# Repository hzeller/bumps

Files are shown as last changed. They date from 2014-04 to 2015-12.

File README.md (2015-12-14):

Bumps
=====

> BeagleBone Universal Multi Pololu Steppers

BeagleBone Black cape for [BeagleG][beagleg-url]; using 5 stepper driver modules
from Pololu.

Bumps is an board to work together with [BeagleG][beagleg-url], a fast
GCode system for CNC/3D printers and one of the first making use of the PRU
of the Beaglebone Black for extremely fast step generation.

Find the current version from June 2015 [shared on OshPark][osh-bumps1]. Or use
the [Gerber files](./gerbers/bumps-gerbers.zip) directly.

### Version History

  * Version 0.1 March 2014 ; 5 Stepper drivers, 2 Power PWMs, 2 small PWM, 2 aux outputs.
  * Version 0.2 June 2015; small revision of otherwise great first board (fix a missing pullup and wrong solder-mask at one place).

### Current work
Work in progress on 0.3 hardware update.

Version 0.3 is work in progress with some changed FETs and other little changes
(see illustration below) but also there is a bigger change
(in branch drv8825-direct) work in progress to directly use the drv8825
drivers without Pololu modules.

Features
   * Simple, mostly passive board with cheap components.
   * Single supply; no separate 5V needed:
      * 5V switching supply to power the BeagleBone from motor voltage (12-36V).
      * Local 3.3V power supply to not put any strain on BBB 3.3V
   * 5 slots for [Pololu-compatible][pololu-url] stepper driver boards.
   * 1 Emergency switch input, directly wired to hardware-reset stepper drivers.
   * 2 high power PWM (Motor voltage, ~20A)
   * 2 Open Collector PWM for smaller loads (Up to 20V, ~2A)
   * 2 Open Collector Auxilliary Outputs (Up to 20V, ~2A)
   * 3 endswitch inputs.
   * 3 temperature sensor inputs.

The following illustrations represent the current work in progress:

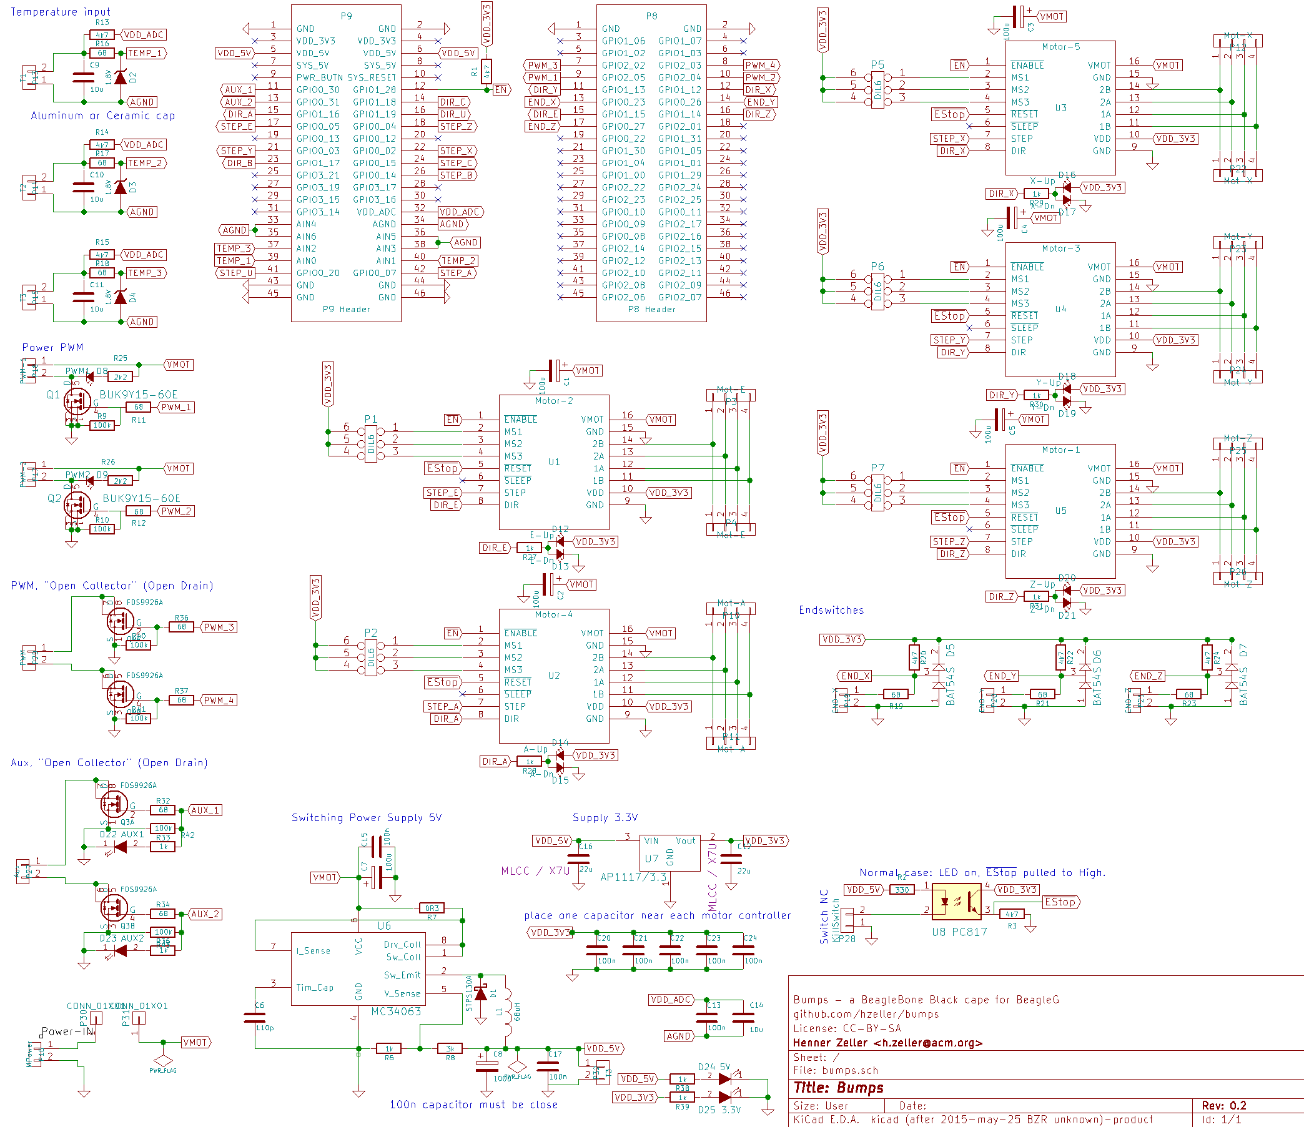
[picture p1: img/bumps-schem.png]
Schematic

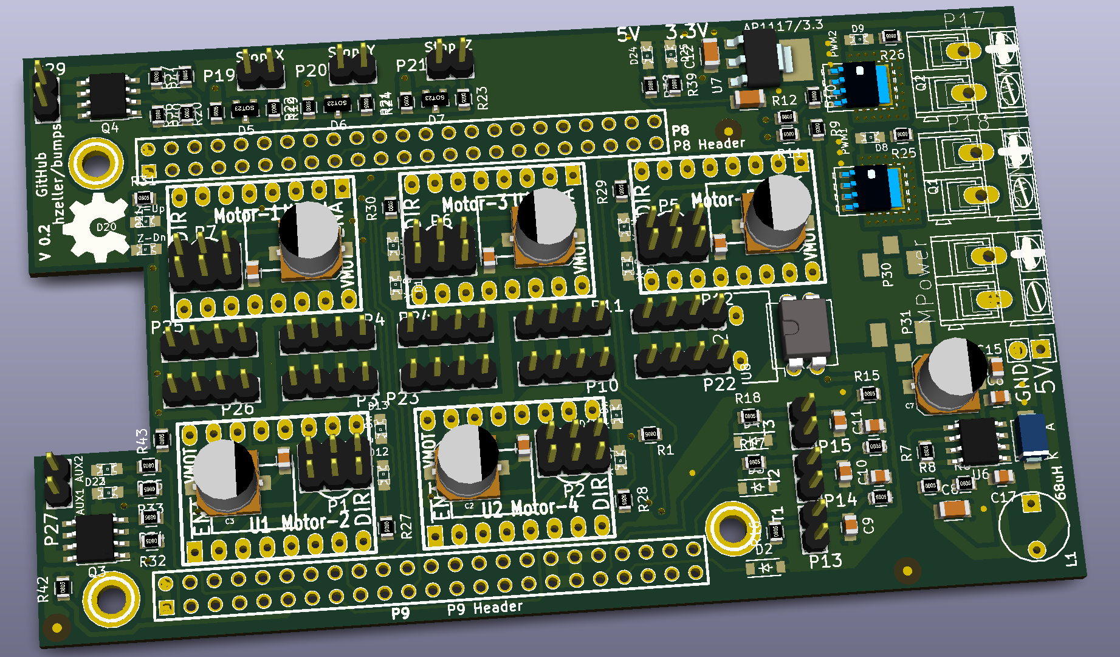
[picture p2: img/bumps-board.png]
Board


In real life, the March 2014 version (essentially identical to the June 2015
version):

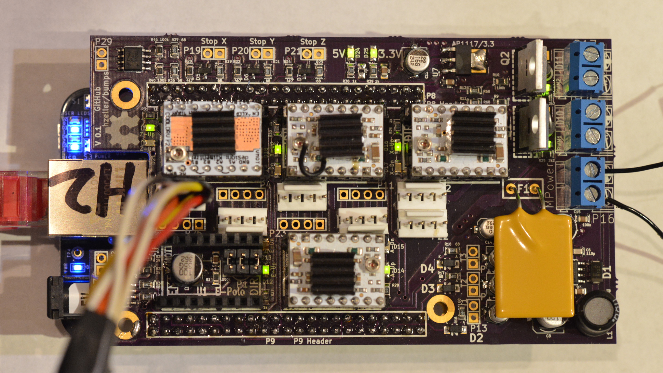
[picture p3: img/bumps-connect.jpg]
Assembled


  * Board fabbed by http://oshpark.com/
  * Solder paste dispensed with http://github.com/jerkey 's 3D printer, using
	a program to translate a KiCAD file to GCode (https://github.com/hzeller/rpt2paste )
	.. the whole thing made it to Hackaday:
	http://hackaday.com/2014/04/02/dispensing-solder-paste-with-a-3d-printer/
  * Assembled using a self-made vacuum tweezer
	https://plus.google.com/u/0/+HennerZeller/posts/b3NbB7NzQcM
  * Early test of the system http://youtu.be/hIEY9077D64

[beagleg-url]: https://github.com/hzeller/beagleg
[pololu-url]: http://www.pololu.com/product/1182
[schem]: https://github.com/hzeller/bumps/raw/master/img/bumps-schem.png
[board]: https://github.com/hzeller/bumps/raw/master/img/bumps-board.png
[assembled]: https://github.com/hzeller/bumps/raw/master/img/bumps-connect.jpg
[osh-bumps1]: https://oshpark.com/shared_projects/zIXfRqDE

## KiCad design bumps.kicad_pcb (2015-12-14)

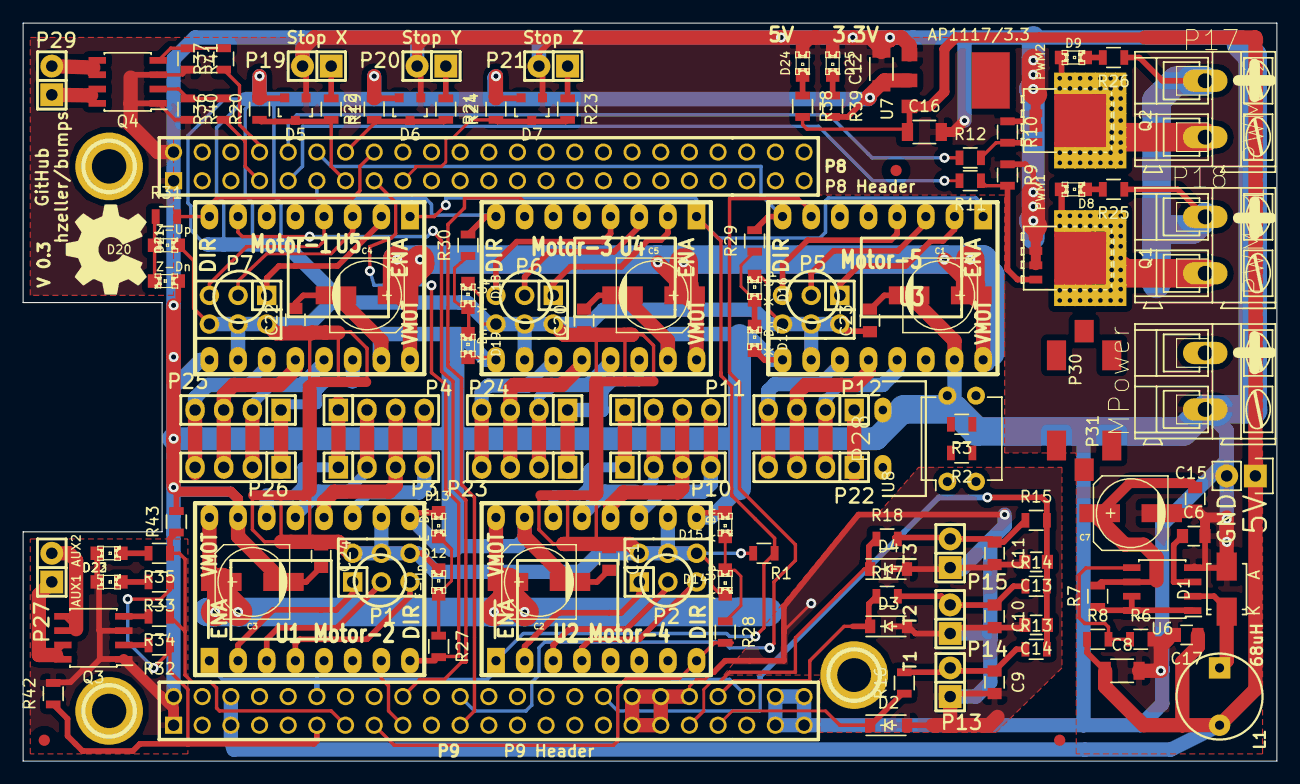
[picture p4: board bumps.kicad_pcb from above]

Board: 2 copper layers, 111.1 x 65.4 mm, 134 parts (0 on the bottom side), 101 nets.

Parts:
C1, C2, C3, C4, C5, C7: 100u; c_elec_6.3x7.7
C6: 110p; C_0805
C8: 100u; C_1206
C9, C10, C11, C14: 10u; C_0805
C12, C16: 22u; C_1206
C13, C15, C17, C20, C21, C22, C23, C24: 100n; C_0805
D1: STPS130A; Diode-SMA_Standard
D2, D3, D4: 1.8V; SOD-123
D5, D6, D7: BAT54S; SOT-23
D8: PWM1; LED-0805
D9: PWM2; LED-0805
D12: E-Up; LED-0805
D13: E-Dn; LED-0805
D14: A-Up; LED-0805
D15: A-Dn; LED-0805
D16: X-Up; LED-0805
D17: X-Dn; LED-0805
D18: Y-Up; LED-0805
D19: Y-Dn; LED-0805
D20: Z-Up; LED-0805
D21: Z-Dn; LED-0805
D22: AUX1; LED-0805
D23: AUX2; LED-0805
D24: 5V; LED-0805
D25: 3.3V; LED-0805
L1: 68uH; INDUCTOR_V
M1, M2, M3: CONN_1; 1pin
P1, P2, P5, P6, P7: DIL6; Pin_Header_Straight_2x03
P3, P4: Mot-E; Pin_Header_Straight_1x04
P8: P8 Header; PIN_ARRAY_23X2
P9: P9 Header; PIN_ARRAY_23X2
P10, P11: Mot-A; Pin_Header_Straight_1x04
P12, P22: Mot-X; Pin_Header_Straight_1x04
P13: T1; Pin_Header_Straight_1x02
P14: T2; Pin_Header_Straight_1x02
P15, P32: T3; Pin_Header_Straight_1x02
P16: MPower; AK300-2
P17: PWM-2; AK300-2
P18: PWM-1; AK300-2
P19: END-X; Pin_Header_Straight_1x02
P20: END-Y; Pin_Header_Straight_1x02
P21: END-Z; Pin_Header_Straight_1x02
P23, P24: Mot-Y; Pin_Header_Straight_1x04
P25, P26: Mot-Z; Pin_Header_Straight_1x04
P27: Aux; Pin_Header_Straight_1x02
P28: KillSwitch; WideHeader
P29: PWM; Pin_Header_Straight_1x02
P30, P31: CONN_01X01; FuseBlade
Q1, Q2: BUK9Y15-60E; SOT-669_LFPAK_ThermalVias-1
Q3, Q4: FDS9926A; SOIC-8_3.9x4.9mm_Pitch1.27mm
R1, R3, R13, R14, R15, R20, R22, R24: 4k7; R_0805
R2: 330; R_0805
R6, R27, R28, R29, R30, R31, R33, R35, R38, R39: 1k; R_0805
R7: 0R3; R_0805
R8: 3k; R_0805
R9, R10, R40, R41, R42, R43: 100k; R_0805
R11, R12, R16, R17, R18, R19, R21, R23, R32, R34, R36, R37: 68; R_0805
R25, R26: 2k2; R_0805
U1: Motor-2; POLOLU
U2: Motor-4; POLOLU
U3: Motor-5; POLOLU
U4: Motor-3; POLOLU
U5: Motor-1; POLOLU
U6: MC34063; SOIC-8_3.9x4.9mm_Pitch1.27mm
U7: AP1117/3.3; SOT-223-3
U8: PC817; DIP-4_W7.62mm

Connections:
AGND: C9.2, C10.2, C11.2, C13.2, C14.2, D2.2, D3.2, D4.2, P9.33, P9.34, P9.35, P9.36, P9.38, P13.1, P14.1, P15.1
AUX_1: P9.11, R32.1, R33.1, R42.1
AUX_2: P9.13, R34.1, R35.1, R43.1
DIR_A: P9.15, R28.2, U2.8
DIR_E: P8.15, R27.2, U1.8
DIR_X: P8.12, R29.2, U3.8
DIR_Y: P8.11, R30.2, U4.8
DIR_Z: P8.16, R31.2, U5.8
END_X: D5.3, P8.13, R19.2, R20.1
END_Y: D6.3, P8.14, R21.2, R22.1
END_Z: D7.3, P8.17, R23.2, R24.1
GND: C1.2, C2.2, C3.2, C4.2, C5.2, C6.2, C7.2, C8.2, C12.2, C15.2, C16.2, C17.2, C20.2, C21.2, C22.2, C23.2, C24.2, D1.2, D5.1, D6.1, D7.1, D13.1, D15.1, D17.1, D19.1, D21.1, D22.1, D23.1, D24.1, D25.1, P8.1, P8.2, P9.1, P9.2, P9.43, P9.44, P9.45, P9.46, P16.2, P19.2, P20.2, P21.2, P28.1, P32.2, Q1.1, Q1.2, Q1.3, Q2.1, Q2.2, Q2.3, Q3.1, Q3.3, Q4.1, Q4.3, R3.2, R6.2, R9.1, R10.1, R40.2, R41.2, R42.2, R43.2, U1.9, U1.15, U2.9, U2.15, U3.9, U3.15, U4.9, U4.15, U5.9, U5.15, U6.4, U7.1
unnamed: C6.1, U6.3
unnamed: C9.1, P13.2, R13.1, R16.2
unnamed: C10.1, P14.2, R14.1, R17.2
unnamed: C11.1, P15.2, R15.1, R18.2
unnamed: D1.1, L1.1, U6.2
unnamed: D8.1, P18.2, Q1.5
unnamed: D8.2, R25.2
unnamed: D9.1, P17.2, Q2.5
unnamed: D9.2, R26.2
unnamed: D12.1, D13.2, R27.1
unnamed: D14.1, D15.2, R28.1
unnamed: D16.1, D17.2, R29.1
unnamed: D18.1, D19.2, R30.1
unnamed: D20.1, D21.2, R31.1
unnamed: D22.2, R33.2
unnamed: D23.2, R35.2
unnamed: D24.2, R38.1
unnamed: D25.2, R39.1
unnamed: P1.1, U1.2
unnamed: P1.2, U1.3
unnamed: P1.3, U1.4
unnamed: P2.1, U2.2
unnamed: P2.2, U2.3
unnamed: P2.3, U2.4
unnamed: P3.1, P4.1, U1.14
unnamed: P3.2, P4.2, U1.13
unnamed: P3.3, P4.3, U1.12
unnamed: P3.4, P4.4, U1.11
unnamed: P5.1, U3.2
unnamed: P5.2, U3.3
unnamed: P5.3, U3.4
unnamed: P6.1, U4.2
unnamed: P6.2, U4.3
unnamed: P6.3, U4.4
unnamed: P7.1, U5.2
unnamed: P7.2, U5.3
unnamed: P7.3, U5.4
unnamed: P10.1, P11.1, U2.14
unnamed: P10.2, P11.2, U2.13
unnamed: P10.3, P11.3, U2.12
unnamed: P10.4, P11.4, U2.11
unnamed: P12.1, P22.1, U3.14
unnamed: P12.2, P22.2, U3.13
unnamed: P12.3, P22.3, U3.12
unnamed: P12.4, P22.4, U3.11
unnamed: P16.1, P30.1
unnamed: P19.1, R19.1
unnamed: P20.1, R21.1
unnamed: P21.1, R23.1
unnamed: P23.1, P24.1, U4.14
unnamed: P23.2, P24.2, U4.13
unnamed: P23.3, P24.3, U4.12
unnamed: P23.4, P24.4, U4.11
unnamed: P25.1, P26.1, U5.14
unnamed: P25.2, P26.2, U5.13
unnamed: P25.3, P26.3, U5.12
unnamed: P25.4, P26.4, U5.11
unnamed: P27.1, Q3.7, Q3.8
unnamed: P27.2, Q3.5, Q3.6
unnamed: P28.2, U8.2
unnamed: P29.1, Q4.7, Q4.8
unnamed: P29.2, Q4.5, Q4.6
unnamed: Q1.4, R9.2, R11.1
unnamed: Q2.4, R10.2, R12.2
unnamed: Q3.2, R32.2
unnamed: Q3.4, R34.2
unnamed: Q4.2, R36.2, R40.1
unnamed: Q4.4, R37.2, R41.1
unnamed: R2.2, U8.1
unnamed: R6.1, R8.2, U6.5
unnamed: R7.1, U6.1, U6.7, U6.8
PWM_1: P8.9, R11.2
PWM_2: P8.10, R12.1
PWM_3: P8.7, R36.1
PWM_4: P8.8, R37.1
STEP_A: P9.42, U2.7
STEP_E: P9.17, U1.7
STEP_X: P9.22, U3.7
STEP_Y: P9.21, U4.7
STEP_Z: P9.18, U5.7
TEMP_1: D2.1, P9.39, R16.1
TEMP_2: D3.1, P9.40, R17.1
TEMP_3: D4.1, P9.37, R18.1
VDD_3V3: C12.1, C20.1, C21.1, C22.1, C23.1, C24.1, D5.2, D6.2, D7.2, D12.2, D14.2, D16.2, D18.2, D20.2, P1.4, P1.5, P1.6, P2.4, P2.5, P2.6, P5.4, P5.5, P5.6, P6.4, P6.5, P6.6, P7.4, P7.5, P7.6, R1.2, R20.2, R22.2, R24.2, R39.2, U1.10, U2.10, U3.10, U4.10, U5.10, U7.2, U8.4
VDD_5V: C8.1, C16.1, C17.1, L1.2, P9.5, P9.6, P32.1, R2.1, R8.1, R38.2, U7.3
VDD_ADC: C13.1, C14.1, P9.32, R13.2, R14.2, R15.2
VMOT: C1.1, C2.1, C3.1, C4.1, C5.1, C7.1, C15.1, P17.1, P18.1, P31.1, R7.2, R25.1, R26.1, U1.16, U2.16, U3.16, U4.16, U5.16, U6.6
~EN: P9.12, R1.1, U1.1, U2.1, U3.1, U4.1, U5.1
~EStop: R3.1, U1.5, U2.5, U3.5, U4.5, U5.5, U8.3

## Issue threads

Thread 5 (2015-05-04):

Don't have two but just one header per motor output

hzeller, 2015-05-04:
The tight packing does not really allow to solder in two molex connectors anyway, so just have one per motor output and have them all in one line not offset.

Also: number them through motor 1, motor 2, ...  which makes it easier for the axis-mapping explanation.

Don't name the pololus X, Y, Z etc, as this is not accurate anymore, just call it channel 1, channel 2 or ch-1, ch-2 or something.

hzeller, 2015-06-03:
Two is probably ok, but they should go in a straight line. That way, it is possible to mount an edge-connector plug.

Closed 2015-06-03.

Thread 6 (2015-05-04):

Possibly have separate input for 5V.

hzeller, 2015-05-04:
If we choose to not populate the motor voltage->5V DC/DC converter (e.g. because we have a motor voltage higher than 40V which is the limit for the 34063.

(todo: should we consider a different DC/DC converter ?)

Closed 2015-06-07.

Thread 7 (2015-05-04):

Make the 10uF analog input capacitors 0805 ceramics

hzeller, 2015-05-04:
We need low voltage and ceramics are better (and less pain to solder) than aluminum caps anyway.

Closed 2015-06-03.

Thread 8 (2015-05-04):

Doublecheck footprint for 100uF driver caps - size works for up to 63V caps ?

hzeller, 2015-05-04:
If we want to operate the drivers with higher voltage (DRV8825 can do up to 45V), the caps should do that. IIRC, the current ones are 35V but we'd need 50V or 63V types here - see if that footprint can do it.

hzeller, 2015-06-03:
Yes.
We also need maximum of 9mm height constraint to fit between connectors.

There is Digikey PCE5024CT-ND which is 6.3mm diameter (current footprint) and 8mm high for 50V and rated 2000h@105C. A winner :)

No board change needed.

Closed 2015-06-03.

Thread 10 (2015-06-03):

PWM on bogus pins

hzeller, 2015-06-03:
The initial choice while getting BUMPS v0.1 out to connect the PWM FETs to timer signals is wrong. We want the EHRPWM pins.
This will need some re-shuffling of some pins.
Ah well ... the number of people using this board is still small.

hzeller, 2015-12-14:
The timer pins work just fine.

Closed 2015-12-14.

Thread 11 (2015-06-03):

PWM on bogus pins

hzeller, 2015-06-03:
The initial choice while getting BUMPS v0.1 out to connect the PWM FETs to timer signals is wrong. We want the EHRPWM pins.
This will need some re-shuffling of some pins.
Ah well ... the user base of three of this board is still small :)

Closed 2015-06-03.

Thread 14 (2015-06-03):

Emergency stop triggering reset

hzeller, 2015-06-03:
If possible in v0.2, we should have an emergency switch input, that takes pulls !RESET on the motor drivers.

Bonus points if we can get that signal into a GPIO.
Extra bonus points if we can also set reset (which is a good thing to have after homing).
Super extra bonus points if the input is protected by an optocoupler, so that we don't have logic inputs connected to long external wires.
(all these bonus points probably won't make it in this revision as routing might be quite challenging at this point).

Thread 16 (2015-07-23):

Discussion Thread

scottjgibson, 2015-07-23:
Hi; sorry this isn't an issue so much as a question regarding discussion about the development of this project.  It's pretty similar to what I have been working on but your implementation is much more refined.

I havn't found any external threads discussing the development of this board; is there one?  Would you be able to upload the gerbers for this project so I can order some V0.2 boards?

Scott

hzeller, 2015-10-21:
Hi - sorry, I think I missed this message.

The previous version I didn't provide as Gerbers, as there are some little things that wouldn't work (the big FETs were connected to the wrong pins) ... unfortunately, the second version is not ready yet as I was swamped with other projects. I hope to get to work on it soon again.

If you really want to try to older version, I could probably create gerberse for it.

hzeller, 2015-12-14:
As you can see, I only get time every now and then to work on the board as the old works quite nicely so far. Anyway, this coming month I have more time on the weekends to get more work done.

There are two things going on w.r.t. to the next version of the Bumps board: one is the relatively small improvement as seen in the current front-page 3D rendering (but it is not completely routed yet), another version is to actually use the driver chips directly. Both versions are work in progress.

I have now shared the previous version (which works perfectly fine except maybe one smallish resister to add) on OshPark https://oshpark.com/shared_projects/TYmqzM19

hzeller, 2015-12-14:
I have now share the version from June 2015 with smallish improvements before the larger (still ongoing) refactorings. Find it under https://oshpark.com/shared_projects/zIXfRqDE
Also, the gerbers are now in the `gerbers/` subdirectory.

sedurCode, 2021-08-29:
Hi, sorry to bother you.
Is this project still current / buildable?
I only ask because its really old (replicape has come and gone since the last commit).
Cheers

jerkey, 2022-01-08:
>

I'm about to find out!  I'm planning on using it to control a Quick Circuit 5000, which is an XY CNC machine with a solenoid for Z axis.  It's the ultimate overkill, but I think it will be fun.

Did you try to use it since your comment, or have you picked something else?

hzeller, 2022-01-08:
The project is still active in the sense that the board is still in regular use (it is just in my CNC machine); however I have not made a new version since then.
It should still be buildable and it will work with BeagleG on a Beagleboard, however the old KiCAD version that I used for this might make it harder to import.

I am currently working on re-vamping BeagleG to also run on other platforms and with that, I am going to design a new board, @sedurCode .

sedurCode, 2022-02-15:
Psyched to hear about a new board! @hzeller

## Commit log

2014-02-02 Init working on a BeagleBone Pololu driver board
    [bumps.sch]
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2014-02-02 added bumps.mod footprints file and set footprints in schematic
    [bumps.sch]
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2014-02-02 added board in kicad 2012-oct-18 and placed parts and board edges and ethernet cutout
    [bumps.brd]
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2014-02-02 added lots of traces AND SWAPPED POSITIONS OF TWO POLOLUS
    [bumps.brd]
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2014-02-02 o Add voltage regulator: generate 5V out of motor voltage.
    [bumps.sch]
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2014-02-02 o Add output capacitor for 5V supply. o Give values to pololu input caps.
    [bumps.sch]
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2014-02-02 o Nicer layout of PWM circuit. o Make sure that PWM FET is pulled down properly and protect BBB output from Gate capacitor switching current.
    [bumps.sch]
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2014-02-04 o Add analog inputs with input protection. o add input protection to end switches. o Add LDO to create a local 3.3V from 5V; use that everywhere, don't use 3.3V provided by BBB o Add LEDs to heater P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
    [bumps.sch]
2014-02-04 o Remove footprint overlay for new components. o Update schematic image.
    [bumps.sch]
2014-02-04 o Make wiring of temp-sensor look less crowded. o add testpoints for 3.3V and 5V o Ground all the BBB grounds.
    [bumps.sch]
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2014-02-08 o Make labels not overlap each other (50mil text size instead of 60mil).
    [bumps.sch]
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2014-02-17 o Separate out the two connectors for motors. o Add free-running diode for PWM connector.
    [bumps.sch]
2014-02-17 o Direction LEDs o Footprints changed. o instad of 120u, use 100u for keeping the BOM small.
    [bumps.sch]
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2014-02-17 o Add 100n for VMOT in to 34063
    [bumps.sch]
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2014-02-22 o turn around micro-step jumper headers. o more appropriate LED footprints.
    [bumps.kicad_pcb, bumps.sch]
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2014-03-02 o More placing. o Add Open Collector AUX and PWM for independent use. o Re-arrange end-switch for easier placement.
    [bumps.kicad_pcb, bumps.sch]
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2014-03-03 o First routings. o Update README, schematic image.
    [bumps.kicad_pcb, bumps.sch]
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2014-03-03 o Swap power-in, so that polarity is consistent with PWM outs.
    [bumps.kicad_pcb, bumps.sch]
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2014-03-04 o Add analog ground plane on top layer.
    [bumps.kicad_pcb]
2014-03-04 o Make analog zone more compact, so that we have place to wire through VMOT
    [bumps.kicad_pcb]
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2014-03-04 o A little bit more clearance for traces near ethernet.
    [bumps.kicad_pcb]
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2014-03-04 o Starting 'wire accross board'-puzzle: all the signals that are inconveniently connecting on opposite sides of the board.
    [bumps.kicad_pcb]
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2014-03-05 o some no-op (I think - whatever kicad thought to change).
    [bumps.kicad_pcb]
2014-03-06 changed the ground Zone around C9 C10 C11 (thermistor caps) to 'thermals' to make it easier to solder the caps (buildability issue)
    [bumps.kicad_pcb]
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2014-03-06 o connect power PWM o start GND plane.
    [bumps.kicad_pcb]
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2014-03-06 o Straighten out motor power trace to lower part a bit.
    [bumps.kicad_pcb]
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2014-03-06 add resistors in parallel with aux1 and aux2 LEDs to turn off FETs when not asserted high by CPU
    [bumps.sch]
2014-03-06 change resistor values for 5V and 3.3V LEDs to make them indicators not eye burners
    [bumps.sch]
2014-03-06 change LED resistors and add lots of necessary bypass capacitors
    [bumps.sch]
2014-03-06 fix capacitors on 5V and 3,3V LEDs to be connected properly across resistors
    [bumps.sch]
2014-03-06 o Straighten out some wires (easier to grab for operations) o connect 100K Gate resistor directly to gound. Easier to layout.
    [bumps.sch]
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2014-03-07 o don't use VMOT 100n caps for now.
    [bumps.sch]
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2014-03-07 o fix moved GND pin.
    [bumps.sch]
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2014-03-07 o More copper around pads - fuse - mounting holes.
    [bumps.kicad_pcb]
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2014-03-07 o Move designators around so that they are more readable.
    [bumps.kicad_pcb]
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2014-03-08 o Screwup in screw-terminals: they didn't have a B-Mask (doh), and also had F-paste. Sounds like someone designed that as SMD pad.
    [bumps.kicad_pcb]
2014-03-08 o Add remark that analog input cap can as well be ceramic.
    [bumps.kicad_pcb, bumps.sch]
2014-03-10 o Smallish adpations while finishing the BOM - some improved placements of designators/values on board - use standard 0805 component for capacitor (not the capacitor 0805)
    [bumps.kicad_pcb, bumps.sch]
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2014-03-11 o Simplify fab generation. o include bottom solder mask.
    [bumps.kicad_pcb]
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2015-05-07 o Fix components, that disappeared in the kicad library (CONN_1, CONN_2 and CONN_4 don't exist anymore, they are now CONN_01X01, CONN_01X02 and CONN_01x04). o Connect the new components that inconven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
    [bumps.sch]
2015-06-03 o Re-read net file for board; new version of kicad now removes empty nets.
    [bumps.kicad_pcb]
2015-06-03 o Get rid of 100k pull-down for MS1. Not needed (fixes #9)
    [bumps.kicad_pcb, bumps.sch]
2015-06-03 o Use 10uF ceramic capacitors in analog section. Makes that part more compact and nicer to assemble. Fixes #7
    [bumps.kicad_pcb, bumps.sch]
2015-06-03 o Add 4k7 pullup to ~Enable o Version number on board-text bumped to v0.2 o Addresses 'enable' part of issue #4
    [bumps.kicad_pcb, bumps.sch]
2015-06-03 o Change footprint of power-FET to have the heat-sink on the right side. o Addresses part of issue #4
    [bumps.kicad_pcb, bumps.sch]
2015-06-03 o Rename motor labels from 'Polo X' to 'Motor 1'. The axis assignment is not done in the hardware, but can be freely assigned in the software. So this would be confusing.
    [bumps.kicad_pcb, bumps.sch]
2015-06-03 o Put all motor connectors in a line (not wiggly line anymore) o Have distance between the same motor connectors 0.2" (distance in female dual sided edge connector) o Fixes #5
    [bumps.kicad_pcb]
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2015-06-04 o convert library to .pretty o add DIL-4 for OptoCoupler (Didn't find it in lib?) and 0.2" distance Wide header for the Estop switch. o assignement and import into pcb, but not routed yet. o make a b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
    [bumps.kicad_pcb, bumps.sch]
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2015-06-05 o Adding fuse holder (footprint and schematic). o .. work in progress. Attempt to make things fit.
    [bumps.kicad_pcb, bumps.sch]
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2015-06-06 o Bring to latest state of kicad library. o Now checking in also bumps-cache: learned that it is effectively the 'project library' keeping track of the symbols being used. o (was done in a branch, sq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
    [bumps.kicad_pcb, bumps.sch]
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2015-06-07 o Design for Manufacturing: choose the same kind of diode for the switching power supply and the snubber diode to reduce different component BOM count.
    [bumps.kicad_pcb, bumps.sch]
2015-06-07 o Use BUK9Y43 as power PWM transistor. SMD is easier to solder.
    [bumps.kicad_pcb, bumps.sch]
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2015-06-07 o Have a header for 5V, which could be used as separate 5v input (if DC/DC converter to populated), or as output for smallish loads. Fixes #6
    [bumps.kicad_pcb, bumps.sch]
2015-06-07 o Mirror Power PWM block, so that the connectors align with the other board connectors on the left. o Update revision number in sheets.
    [bumps.kicad_pcb, bumps.sch]
2015-06-11 o Replace some smallish aluminum caps with MLCCs
    [bumps.kicad_pcb, bumps.sch]
2015-06-11 o Don't keep mounting holes on schematic, just make them locked footprints on the board.
    [bumps.kicad_pcb, bumps.sch]
2015-06-11 o More compact 3.3V regulator section to prepare for more endswitch components.
    [bumps.kicad_pcb]
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

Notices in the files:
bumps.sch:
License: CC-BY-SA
